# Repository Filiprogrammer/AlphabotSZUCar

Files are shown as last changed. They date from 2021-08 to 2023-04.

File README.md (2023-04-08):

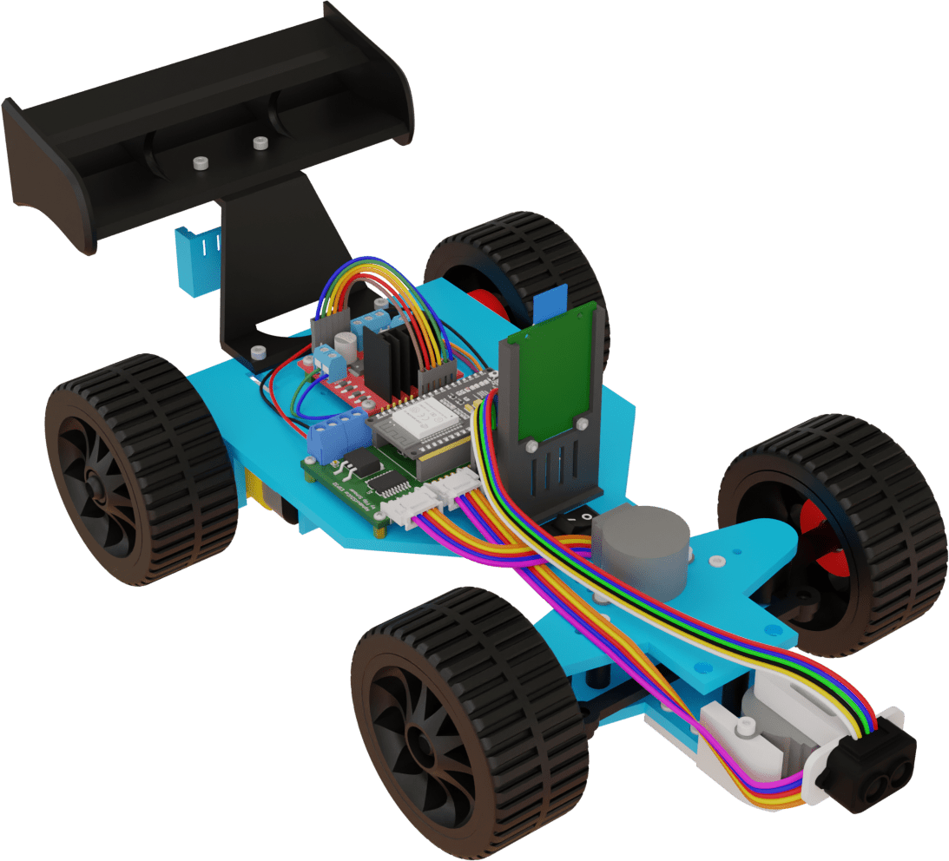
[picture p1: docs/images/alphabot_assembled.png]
Assembled Alphabot


AlphabotSZUCar
==============



The AlphabotSZUCar is a remote-controlled model car with some functions that also let it act autonomously in various ways.

There exist two major variations of this car:

- Controlled by Raspberry Pi 3B/3B+/4B (single-board computer)
- Controlled by ESP32 (microcontroller)

Features
--------

* Communication through WiFi
* Communication through Bluetooth Low Energy
* Remote controlled manual driving
* Obstacle detection & Collision avoidance
* Position and orientation system
* Pathfinding with obstacle avoidance
* Autonomous driving

Building the Alphabot
---------------------

[Alphabot Build Instructions](docs/alphabot_build_instructions.md)

Raspberry Pi variation: Building the software
---------------------------------------------

[Building the software for the Raspberry Pi variation of the Alphabot](docs/alphabot_rpi_software.md)

Emulating the Alphabot
----------------------

[Alphabot Emulation](docs/alphabot_emulation.md)

Connecting to Alphabot with a client
------------------------------------

[Alphabot Client](docs/alphabot_client.md)

Using the Alphabot
------------------

[Alphabot Usage](docs/alphabot_usage.md)

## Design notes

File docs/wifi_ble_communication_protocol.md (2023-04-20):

# 1. WiFi – bit based protocol

All byte sequences (int16, int64...) correspond to the "little-endian" standard.

## 1.1. Packet header

The packet header consists of 1 byte. All following bytes are the payload of the packet.
The last 3 bits (MSB) of the packet header define the protocol version. Currently the only version is 000.

### 1.1.1. Example packet

| Bit 7-5 (MSB) <br> [Version 0] | Bit 4-0 (LSB) <br> [Packet ID 0x01] |
|---|---|
| 0 0 0 | 0 0 0 0 1 |

## 1.2. Requests (Client to Alphabot)

### Speed & Steer (Packet ID: 0x01)

| Field Name | Field Type | Notes |
|---|---|---|
| Speed | int8 | The desired speed (negative values indicate backward driving, positive values indicate forward driving) |
| Steer | int8 | The desired steering direction (negative values indicate left steering, positive values indicate right steering) |

### Calibrate steering (Packet ID: 0x03)

No further data

### Calibrate compass (Packet ID: 0x04)

| Field Name | Field Type | Notes |
|---|---|---|
| Calibration type | uint8 | 0x01 for automatic compass calibration; 0x02 to start manual compass calibration; 0x03 to end manual compass calibration; 0x04 to set compass offset |

### Toggle request (Packet ID: 0x05)

see [3.1. Toggle bit field](#31-toggle---bit-field)

### Ping request (Packet ID: 0x06)

| Field Name | Field Type | Notes |
|---|---|---|
| Timestamp  | int64 | The Unix epoch time in milliseconds when the packet is sent |

### Configure positioning anchors location (Packet ID: 0x07)

| Field Name | Field Type | Notes |
|---|---|---|
| AnchorID | uint8 | The ID of the anchor |
| Position X | int16 | The x coordinate in centimetres |
| Position Y | int16 | The y coordinate in centimetres |

### Set target position for navigation (Packet ID: 0x08)

| Field Name | Field Type | Notes |
|---|---|---|
| Position X | int16 | The x coordinate in centimetres |
| Position Y | int16 | The y coordinate in centimetres |

### Add obstacle (Packet ID: 0x09)

| Field Name | Field Type | Notes |
|---|---|---|
| Position X | int16 | The x coordinate in centimetres |
| Position Y | int16 | The y coordinate in centimetres |
| Width | uint16 | The width in centimetres |
| Height | uint16 | The height in centimetres |

### Remove one obstacle by ID (Packet ID: 0x0A)

| Field Name | Field Type | Notes |
|---|---|---|
| ID | uint16 | ID of the obstacle |

### Remove obstacle by position (Packet ID: 0x0B)

If there are multiple objects in the same position, all of them will be removed.

| Field Name | Field Type | Notes |
|---|---|---|
| Position X | int16 | The x coordinate in centimetres |
| Position Y | int16 | The y coordinate in centimetres |

### Remove all obstacles (Packet ID: 0x0C)

All obstacles (manually added and discovered by the Alphabot) will be removed.

No further data

## 1.3. Responses (Alphabot to client)

### Front distance sensor response (Packet ID: 0x01)

Degree 0 represents the direction, in which the Alphabot is headed towards.
Degree 90 is the right direction.

| Field Name | Field Type | Notes |
|---|---|---|
| Degree | int16 | The degree of the sensor (0-359) |
| Distance | uint16 | The distance in centimetres |

### Positioning response (Packet ID: 0x02)

| Field Name | Field Type | Notes |
|---|---|---|
| Position X | int16 | The x coordinate in centimetres |
| Position Y | int16 | The y coordinate in centimetres |

### Path finding response (Packet ID: 0x03)

| Field Name | Field Type | Notes |
|---|---|---|
| X-start | int8 | X coordinate of the start position in decimeters |
| Y-start | int8 | Y coordinate of the start position in decimeters |
| Path steps data | Path steps data structure | see [Path steps data structure](#33-Path-steps-data-structure) |

### Compass response (Packet ID: 0x04)

The direction is relative to the coordinate system, where +X is right and +Y is down.\
0 degrees indicates the Alphabot is facing in the +X direction.\
90 degrees indicates the Alphabot is facing in the +Y direction.\
180 degrees indicates the Alphabot is facing in the -X direction.\
270 degrees indicates the Alphabot is facing in the -Y direction.

| Field Name | Field Type | Notes |
|---|---|---|
| Degree | int16 | The measured degree (0-359) |

### Ping response (Packet ID: 0x05)

| Field Name | Field Type | Notes |
|---|---|---|
| Timestamp  | int64 | The Unix epoch time in milliseconds when the packet was sent |

### New obstacle registered (Packet ID: 0x06)

| Field Name | Field Type | Notes |
|---|---|---|
| Position X | int16 | The x coordinate in centimetres |
| Position Y | int16 | The y coordinate in centimetres |
| Width | uint16 | The width in centimetres |
| Height | uint16 | The height in centimetres |
| ID | uint16 | The ID of the obstacle |

### Toggle response (Packet ID: 0x07)

The toggle settings get automatically sent upon a new client connection, but they will also be sent if
the Alphabot changes a setting by itself.

see [3.1. Toggle bit field](#31-toggle---bit-field)

### Anchor distance response (Packet ID: 0x08)

| Field Name | Field Type | Notes |
|---|---|---|
| Distance | uint16 | The distance to anchor 0 in centimeters |
| Distance | uint16 | The distance to anchor 1 in centimeters |
| Distance | uint16 | The distance to anchor 2 in centimeters |

### Wheel speed response (Packet ID: 0x09)

| Field Name  | Field Type | Notes |
|---|---|---|
| Speed left  | int8 | The speed of the left wheel in m/s * 100  |
| Speed right | int8 | The speed of the right wheel in m/s * 100 |

### Gyroscope response (Packet ID: 0x0A)

| Field Name | Field Type | Notes |
|---|---|---|
| X-axis | int16 | The speed of the x-axis in degree/s * 10 |
| Y-axis | int16 | The speed of the y-axis in degree/s * 10 |
| Z-axis | int16 | The speed of the z-axis in degree/s * 10 |

### Accelerometer response (Packet ID: 0x0B)

| Field Name | Field Type | Notes |
|---|---|---|
| X-axis | int16 | The acceleration of the x-axis in m/s&#xB2; * 1000 |
| Y-axis | int16 | The acceleration of the y-axis in m/s&#xB2; * 1000 |
| Z-axis | int16 | The acceleration of the z-axis in m/s&#xB2; * 1000 |

### Magnetometer response (Packet ID: 0x0C)

| Field Name | Field Type | Notes |
|---|---|---|
| X-axis | int16 | The magnetic flux density of the x-axis in &#xB5;T * 10 |
| Y-axis | int16 | The magnetic flux density of the y-axis in &#xB5;T * 10 |
| Z-axis | int16 | The magnetic flux density of the z-axis in &#xB5;T * 10 |

### Error message (Packet ID: 0x0D)

| Field Name | Field Type | Notes |
|---|---|---|
| Error ID | uint8 | The error ID, see [3.4.](#34-error-id-format)  |
| Packet header  | uint8 | The packet header that threw the error |
| Payload | uint8 array (0-20) | The payload of the packet that threw the error |

### Back distance sensor response (Packet ID: 0x0E)

Degree 0 represents the opposite direction, in which the Alphabot is headed towards.
Degree 90 is the left direction.

| Field Name | Field Type | Notes |
|---|---|---|
| Degree | int16 | The degree of the sensor (0-359) |
| Distance | uint16 | The distance in centimetres |

# 2. BLE Protocol

### BLE_CHAR_DRIVE_STEER (UUID: a04295f7-eaa8-4536-b3a4-4e7ae4d72dc2)

| Field Name | Field Type | Notes |
|---|---|---|
| Speed | int8 | The desired speed (negative values indicate backward driving, positive values forward driving) |
| Steer | int8 | The desired steering direction (negative values indicate left steering, positive values indicate right steering) |

### BLE_CHAR_PINGCLIENT	(UUID: 117ad3a5-b257-4465-abd4-7dc12a4cf77d)

| Field Name | Field Type | Notes |
|---|---|---|
| Timestamp  | int64 | The Unix epoch time in milliseconds when the packet is sent |

### BLE_CHAR_TOGGLE (UUID: fce001d4-864a-48f4-9c95-de928f1da07b)

| Field Name | Field Type | Notes |
|---|---|---|
| Settings toggle bit field | uint8 | see [3.1.1. Toggle bit field (Settings)](#311-bit-field--1-byte-settings) |
| Logging toggle bit field  | uint8 | see [3.1.2. Toggle bit field (Logging)](#312-bit-field--2-byte-logging) |
| Timestamp | int64 | The Unix epoch time in milliseconds when the packet is sent |

### BLE_CHAR_SENSOR (UUID: 4c999381-35e2-4af4-8443-ee8b9fe56ba0)

see [3.2. Sensor packets](#32-sensor--packets-ble-only)

### BLE_CHAR_TARGET_NAVI (UUID: f56f0a15-52ae-4ad5-bfe1-557eed983618)

| Field Name | Field Type | Notes |
|---|---|---|
| Position X | int16 | The x coordinate in centimetres |
| Position Y | int16 | The y coordinate in centimetres |
| Timestamp  | int64 | The Unix epoch time in milliseconds when the packet is sent |

### BLE_CHAR_CALIBRATE (UUID: d39e8d54-8019-46c8-a977-db13871bac59)

| Field Name | Field Type  | Notes |
|---|---|---|
| Calibration Type | int8 | 0x00 to calibrate steering; 0x01 for automatic compass calibration; 0x02 to start manual compass calibration; 0x03 to end manual compass calibration; 0x04 to set compass offset |
| Timestamp | int64 | The Unix epoch time in milliseconds when the packet is sent |

### BLE_CHAR_ADD_OBSTACLE (UUID: 60db37c7-afeb-4d40-bb17-a19a07d6fc95)

At first position, width and height is sent by the client, the Alphabot will answer with the data and the ID.

| Field Name | Field Type | Notes |
|---|---|---|
| Timestamp  | int64 | The Unix epoch time in milliseconds when the packet is sent |
| Position X | int16 | The x coordinate in centimetres |
| Position Y | int16 | The y coordinate in centimetres |
| Width | uint16 | The width in centimetres |
| Height | uint16 | The height in centimetres |
| ID | uint16 | The ID of the obstacle (gets set by the Alphabot) |

### BLE_CHAR_REMOVE_OBSTACLE (UUID: 6d43e0df-682b-45ef-abb7-814ecf475771)

Obstacles can be removed either by ID or by position.
If the characteristic is 0 bytes long, ALL obstacles will be removed.
If the characteristic is 10 bytes long, the value is interpreted as the obstacle ID.
If the characteristic is 12 bytes long, the values are interpreted as the position.
The Alphabot will send the corresponding packet when the removal of obstacles is completed.
If there are multiple objects on the same position, all of them will be removed.

| Field Name | Field Type | Notes |
|---|---|---|
| Timestamp  | int64 | The Unix epoch time in milliseconds when the packet is sent |
| ID | uint16 | The ID of the obstacle |

#### OR

| Field Name | Field Type | Notes |
|---|---|---|
| Timestamp  | int64 | The Unix epoch time in milliseconds when the packet is sent |
| Position X | int16 | The x coordinate in centimetres |
| Position Y | int16 | The y coordinate in centimetres |

### BLE_CHAR_PATH_FINDING (UUID: 8dad4c9a-1a1c-4a42-a522-ded592f4ed99)

| Field Name | Field Type | Notes |
|---|---|---|
| X-start | int8 | X coordinate of the start position in decimeters |
| Y-start | int8 | Y coordinate of the start position in decimeters |
| Path steps data | Path steps data structure | see [Path steps data structure](#33-Path-steps-data-structure) |

### BLE_CHAR_ANCHOR_LOCATIONS (UUID: 8a55dd30-463b-40f6-8f21-d68efcc386b2)

| Field Name | Field Type | Notes |
|---|---|---|
| Timestamp  | int64 | The Unix epoch time in milliseconds when the packet is sent |
| Position X | int16 | The x coordinate in centimetres of anchor 0 |
| Position Y | int16 | The y coordinate in centimetres of anchor 0 |
| Position X | int16 | The x coordinate in centimetres of anchor 1 |
| Position Y | int16 | The y coordinate in centimetres of anchor 1 |
| Position X | int16 | The x coordinate in centimetres of anchor 2 |
| Position Y | int16 | The y coordinate in centimetres of anchor 2 |

### BLE_CHAR_ANCHORS_DISTANCES (UUID: 254492a2-9324-469b-b1e2-4d4590972c35)

| Field Name | Field Type | Notes |
|---|---|---|
| Distance | uint16 | The distance to anchor 0 in centimetres |
| Distance | uint16 | The distance to anchor 1 in centimetres |
| Distance | uint16 | The distance to anchor 2 in centimetres |

### BLE_CHAR_IMU (UUID: 93758afa-ce6f-4670-9562-ce92bda84d49)

| Field Name | Field Type | Notes |
|---|---|---|
| Type | int8 | Indicates whether the packet is a gyroscope-package (value 0), an accelerometer-package (value 1), or an magnetometer-package (value 2) |
| x-Axis | int16 | The value of the x-Axis |
| y-Axis | int16 | The value of the y-Axis |
| z-Axis | int16 | The value of the z-Axis |

### BLE_CHAR_WHEEL_SPEED (UUID: 8efafa16-15de-461f-bde1-493261201e2b)

| Field Name  | Field Type | Notes |
|---|---|---|
| Speed left  | int8 | The speed of the left wheel in m/s * 100  |
| Speed right | int8 | The speed of the right wheel in m/s * 100 |

### BLE_CHAR_ERROR (UUID: dc458f08-ea3e-4fe1-adb3-25c840be081a)

If the original payload was 19 or 20 bytes long, the last one or two bytes won't be shown.

| Field Name | Field Type | Notes |
|---|---|---|
| Error ID | uint8 | The error ID, see [3.4.](#34-error-id-format) |
| BLE CHAR ID | uint8 | The first byte of the BLE characteristic UUID that threw the error |
| Payload | uint8 array (0-18) | The payload of the packet that threw the error |

# 3. Bit fields

## 3.1. Toggle - Bit field

In the WiFi protocol, the packet 0x05 is followed by a 2-byte bit field.
In the BLE protocol it is a characteristic which is 10 bytes in size, because the timestamp (8 bytes) is sent right after the actual bit field (2 bytes)
This bit field allows various settings to be switched on or off. If a 0 is sent,
that setting is going to be deactivated, if a 1 is sent it is going to be activated.
General settings are sent in the 1st byte. 
The 2nd byte changes certain logging options.

### 3.1.1. Bit field – 1. Byte (Settings)

| Bit 7 (MSB) | Bit 6 | Bit 5 | Bit 4 | Bit 3 | Bit 2 | Bit 1 | Bit 0 (LSB) |
|---|---|---|---|---|---|---|---|
| Invite | Positioning | Collision Avoidance | Navigation-Mode | Explore-Mode | not used | not used | not used |

### 3.1.2. Bit field – 2. Byte (Logging)

| Bit 7 (MSB) | Bit 6 | Bit 5 | Bit 4 | Bit 3 | Bit 2 | Bit 1 | Bit 0 (LSB) |
|---|---|---|---|---|---|---|---|
| Positioning | Obstacle distance | Pathfinder path | Compass direction | Anchor distances | Wheel speed | Inertial Measurement Unit | not used |

## 3.2. Sensor – Packets (BLE only)

The first two bytes describe the sensor types that will follow. Then the payload of these packets will follow. There can be multiple sensor responses sent at a time. The following responses can be sent in one packet:

### Example bit stream

In the first byte 0b01 is sent twice, because two front distance sensor packets will follow. The following bits in the first two bytes do not matter in this case, because the bit stream does not contain more sensor data. Byte 2 and 3 represent the payload of the first distance sensor data. Byte 4 and 5 represent the payload of the second distance sensor data.

| Byte 0 | Byte 1 | Byte 2 | Byte 3 | Byte 4 | Byte 5 |
|---|---|---|---|---|---|
| 00000101 | 00000000 | 00000101 | 10000000 | 01100100 | 10000001 |

### Back distance sensor response (Sensor type: 0b00)

Degree 0 represents the opposite direction, in which the Alphabot is headed towards.
Degree 90 is the left direction.

| Field Name | Field Type | Notes |
|---|---|---|
| Degree | int8 | The degree of the sensor (-128-127) |
| Distance | uint8 | The distance in centimetres divided by 2 |

### Front distance sensor response (Sensor type: 0b01)

Degree 0 represents the direction, in which the Alphabot is headed towards.
Degree 90 is the right direction.

| Field Name | Field Type | Notes |
|---|---|---|
| Degree | int8 | The degree of the sensor (-128-127) |
| Distance | uint8 | The distance in centimetres divided by 2 |

### Positioning response (Sensor type: 0b10)

The position will be split into 3 bytes, 12 bit per coordinate

| Field Name | Field Type | Notes |
|---|---|---|
| Position X | int12 | The x coordinate in centimetres |
| Position Y | int12 | The y coordinate in centimetres |

### Compass response (Sensor type: 0b11)

The direction is relative to the coordinate system, where +X is right and +Y is down.\
0 degrees indicates the Alphabot is facing in the +X direction.\
90 degrees indicates the Alphabot is facing in the +Y direction.\
180 degrees indicates the Alphabot is facing in the -X direction.\
270 degrees indicates the Alphabot is facing in the -Y direction.

| Field Name | Field Type | Notes |
|---|---|---|
| Degree | int16 | The measured degree (0-359) |

## 3.3. Path steps data structure

The Path steps data structure contains a list of steps in certain directions which together form a path.
The length of the data structure can be anywhere between 1 to 18 bytes long.
The first 6 bits of the first byte contain the number of the following path steps.
Note that bit 0 refers to the least significant bit.
The path steps are stored such that several entries are within a single byte and sometimes an entry overlaps between multiple bytes.
The first entry is stored in bits 6 and 7 of the first byte and in bit 0 of the second byte.
Bits 1 to 3 of the second byte are the second entry, bits 4 to 6 are the third entry, and so on.
With 3 bits per path step there are 8 possible values. The format of a path step is described in [Path step format](#331-Path-step-format)

### 3.3.1. Path step format

| Encoded value | Direction  |
|---|---|
| 0 | left-up |
| 1 | left |
| 2 | left-down  |
| 3 | up |
| 4 | right-down |
| 5 | down |
| 6 | right-up |
| 7 | right |

### 3.3.2. Example bit stream

The following example shows a possible bit stream of the path finding data. In the [example encoded in bytes](#333-example-encoded-in-bytes) all steps are explained explicitly.

<span style="color:#f53d3d">001000</span>
| <span style="color:#f5993d">001</span>
| <span style="color:#f5f53d">010</span>
| <span style="color:#99f53d">101</span>
| <span style="color:#3df53d">101</span>
| <span style="color:#3df599">100</span>
| <span style="color:#3df5f5">100</span>
| <span style="color:#3d99f5">111</span>
| <span style="color:#3d3df5">111</span>
| 00

### 3.3.3. Example encoded in bytes

<span style="color:#f5993d">01</span><span style="color:#f53d3d">001000</span>
<span style="color:#3df53d">1</span><span style="color:#99f53d">101</span><span style="color:#f5f53d">010</span><span style="color:#f5993d">0</span>
<span style="color:#3df5f5">100</span><span style="color:#3df599">100</span><span style="color:#3df53d">10</span>
00<span style="color:#3d3df5">111</span><span style="color:#3d99f5">111</span>

| Binary value of step | Step direction |
|---|---|
| <span style="color:#f53d3d">001000</span> | Number of path steps = 8 |
| <span style="color:#f5993d">001</span> | left |
| <span style="color:#f5f53d">010</span> | left-down |
| <span style="color:#99f53d">101</span> | down |
| <span style="color:#3df53d">101</span> | down |
| <span style="color:#3df599">100</span> | right-down |
| <span style="color:#3df5f5">100</span> | right-down |
| <span style="color:#3d99f5">111</span> | right |
| <span style="color:#3d3df5">111</span> | right |

## 3.4. Error id format

| Encoded value | Error |
|---|---|
| 0x00 | unknown error |
| 0x01 | unknown protocol |
| 0x02 | known but not supported protocol  |
| 0x03 | unknown packet ID |
| 0x04 | wrong payload |

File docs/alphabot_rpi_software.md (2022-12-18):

# Building the software for the Raspberry Pi variation of the Alphabot

## Prerequisites

Make sure that you have at least 3GB of free storage space.

Make sure that you have installed the following prerequisites:

* Docker - [Docker Engine Install Instructions](https://docs.docker.com/engine/install/)
* parted

Debian:

```console
sudo apt-get install parted
```

Arch Linux:

```console
sudo pacman -Sy parted
```

Fedora:

```console
sudo yum install parted
```

* kpartx

Debian:

```console
sudo apt install kpartx
```

Arch Linux:

```console
sudo pacman -Sy multipath-tools
```

Fedora:

```console
sudo yum install kpartx
```

## Build Image

```console
sudo rpi/sd_image/build.sh
```

## Running on real hardware

Flash rpi/sd_image/raspi_alphabot.img onto an SD card with a size of at least 1GiB. Plug the flashed SD card into your Raspberry Pi 3B/3B+/4B.

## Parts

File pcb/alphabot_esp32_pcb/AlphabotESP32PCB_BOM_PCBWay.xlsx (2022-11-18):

 |  |  | BOM
Item # | *Designator | *Qty | Manufacturer | *Mfg Part # | Description / Value | *Package/Footprint | Type | Your Instructions / Notes
1 | ICMU1 | 1 | TDK InvenSense | ICM-20948 | IMU ACCEL/GYRO/COMPI2C/SPI 24QFN | 24QFN | SMD | Pin 1 is on the left side. It is intentional that there is no pad on the PCB for the exposed die pad on the center of the chip.
2 | C1,C4 | 2 | KEMET | C0603C104K3RAC7013 | CAP CER 0.1uF ±10% 25V X7R | 0603 | SMD
3 | C2 | 1 | KEMET | C0603C106M8PAC7411 | CAP CER 10uF ±20% 10V X5R | 0603 | SMD
4 | ICMC1 | 1 | KEMET | C0805C104K5RAC7411 | CAP CER 0.1uF ±10% 50V X7R | 0805 | SMD
5 | Q1,Q3,Q4 | 3 | ON Semiconductor | BSS138 | MOSFET N-CH 50V 220MA SOT23-3 | SOT-23-3 | SMD
6 | R1 | 1 | Vishay / Dale | CRCW06031K00FKEA | RES 1.0K OHM 1/10W 1% | 0603 | SMD
7 | R2 | 1 | Vishay / Dale | CRCW06032K20FKEA | RES 2.2K OHM 1/10W 1% | 0603 | SMD
8 | R5,R6,R7,R11 | 4 | Vishay / Dale | CRCW060310K0FKEA | RES 10K OHM 1/10W 1% | 0603 | SMD
9 | R9,R10 | 2 | Vishay / Dale | CRCW06034K70FKEA | RES 4.7K OHM 1/10W 1% | 0603 | SMD
10 | U1 | 1 | Microchip Technology / Micrel | MIC5225-1.8YM5-TR | IC REG LINEAR 1.8V 150MA SOT-23-5 | SOT-23-5 | SMD
11 | U2 | 1 | UTD Semiconductor | ULN2803A | SOP-18 DARLINGTON TRANSISTOR ARR | 18-SOP | SMD
12 | U4 | 1 | STMicroelectronics (https://www.mouser.at/manufacturer/stmicroelectronics/) | L7805ACD2T-TR | IC REG LINEAR 5V 1.5A D2PAK | D2PAK | SMD
13 | C3 | 1 | KEMET | C0603C331K5RAC7867 | CAP CER 330PF 50V X7R 0603 | 0603 | SMD

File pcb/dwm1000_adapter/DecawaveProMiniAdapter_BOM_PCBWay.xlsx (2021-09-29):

 |  |  | BOM
Item # | *Ref Des | *Qty | Manufacturer | *Mfg Part # | Description / Value | *Package | Type | Your Instructions / Notes
1 | U1,U2,U3 | 3 | Texas Instruments | SN74LVC2G17DBVRG4 | IC BUF NON-INVERT 5.5V | SOT-23-6 | SMD | Align dot on chip with dot on PCB (pin 1)
2 | C1,C3 | 2 | Wurth Elektronik | 885012206071 | CAP CER 0.1uF ±10% 25V X7R | 0603 | SMD
3 | C2,C4,C5 | 3 | Yageo | CC0603ZRY5V7BB105 | CAP CER 1uF -20%, +80% 16V Y5V | 0603 | SMD
4 | R1 | 1 | Vishay / Dale | CRCW06031K00FKEA | RES 1.0K OHM 1/10W 1% | 0603 | SMD
5 | R2 | 1 | Vishay / Dale | CRCW060310K0FKEA | RES 10K OHM 1/10W 1% | 0603 | SMD
6 | LDO | 1 | Diodes Incorporated | AP7333-33SRG-7 | IC REG LIN 3.3V 300MA SOT23R-3 | SOT-23R-3 | SMD
7 | D1 | 1 | Lite-On Inc. | LTST-C191KGKT | Green 571nm LED Indication - Discrete 2V 0603 | 0603 | SMD
8 | J1 | 1 | TE Connectivity AMP Connectors | 1734035-4 | CONN RCPT USB2.0 MINI B SMD R/A |  | SMD
9 | DWM1000 | 1 | Decawave | DWM1000 | IC RF-Module UWB Transceiver |  | SMD

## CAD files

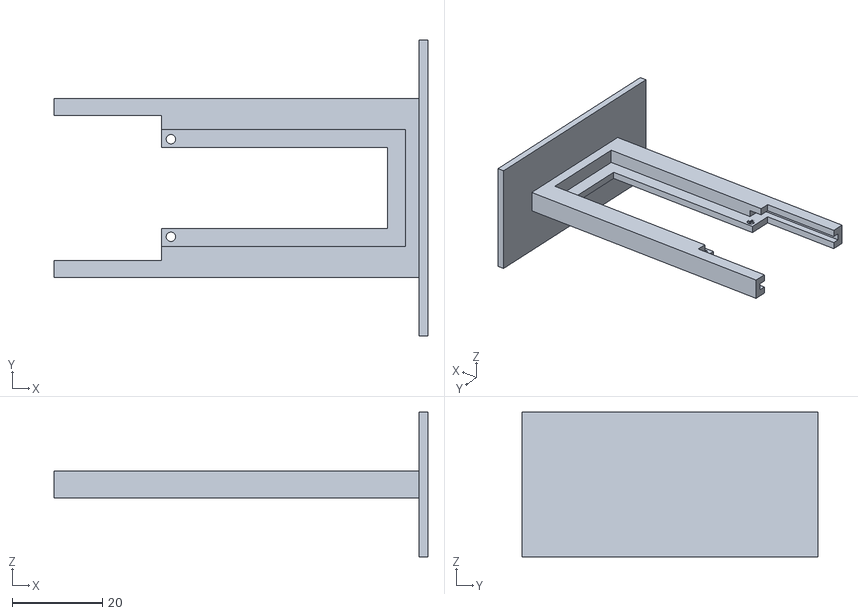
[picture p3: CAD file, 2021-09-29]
stl/dwm1000.anchor.adapter.board.mount.stl
82.8 x 65.6 x 32.0

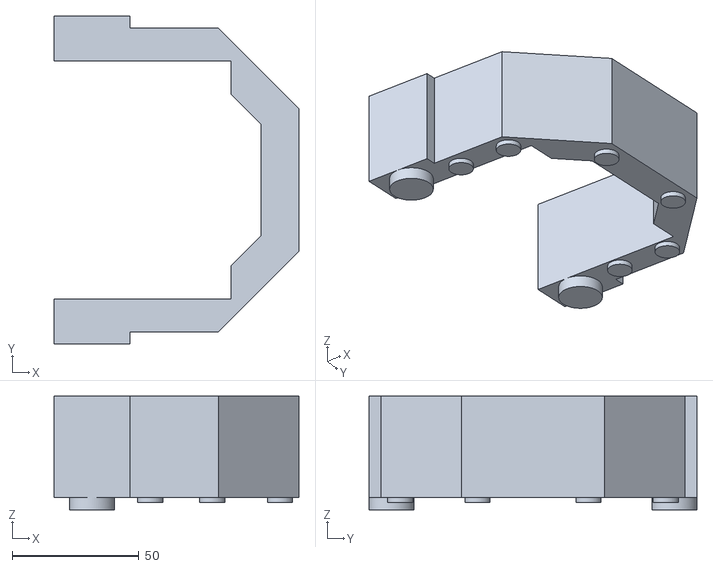
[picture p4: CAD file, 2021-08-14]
stl/stand/alphabot.stand.V3.stl
96.8 x 129.5 x 45.0

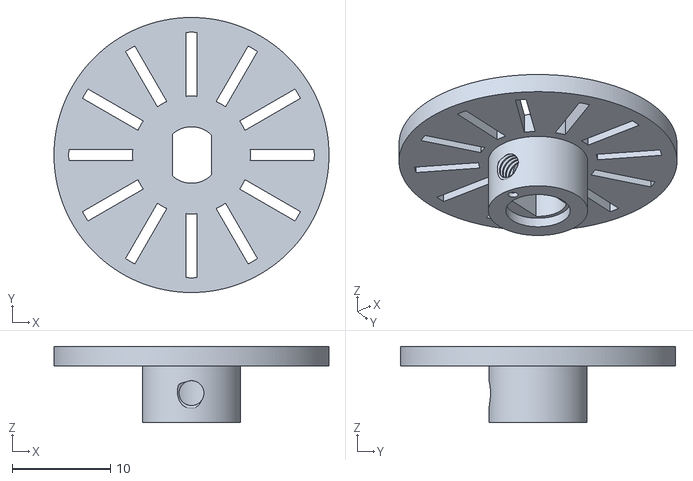
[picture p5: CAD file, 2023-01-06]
stl/vehicle/addon/wheel.encoder.stl
28.0 x 28.0 x 7.75

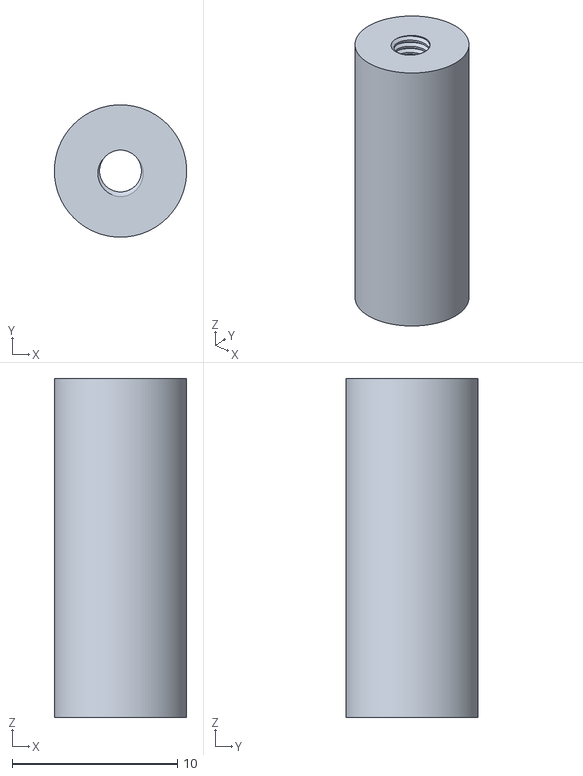
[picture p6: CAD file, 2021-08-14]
stl/vehicle/base/frontwheel.suspension.distance.stl
8.00 x 8.00 x 20.5

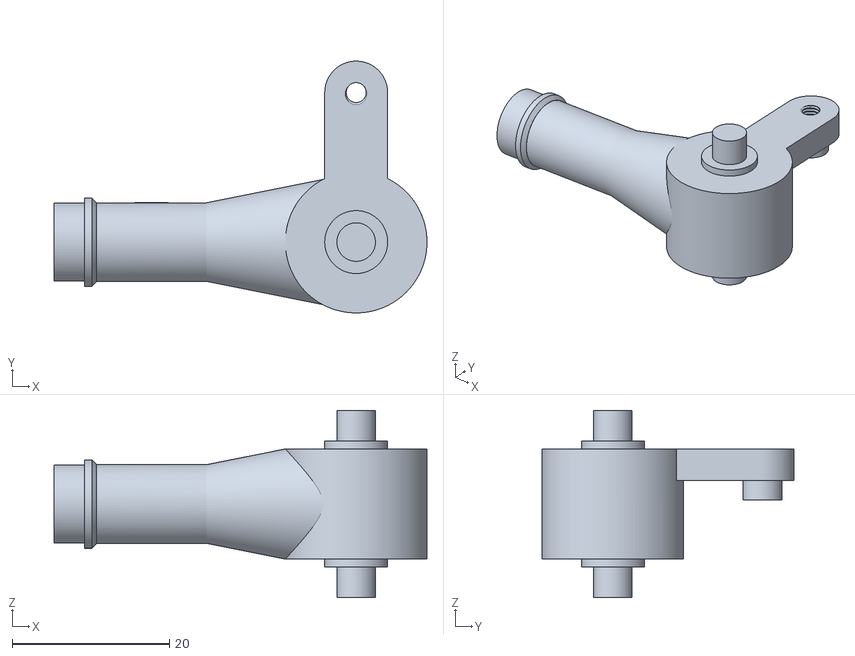
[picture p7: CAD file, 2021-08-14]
stl/vehicle/steering/suspension.right.V4.stl
47.4 x 32.0 x 23.8

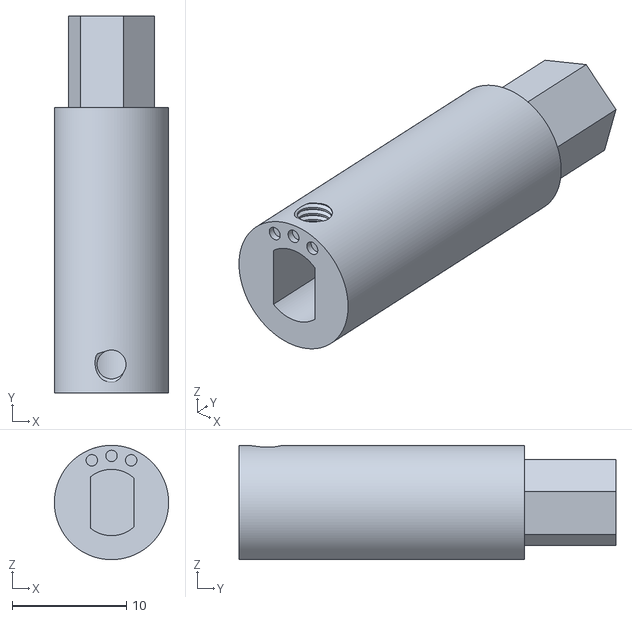
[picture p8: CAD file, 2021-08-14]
stl/vehicle/wheel/rim.axle.back.xl.stl
10.00 x 33.0 x 10.00

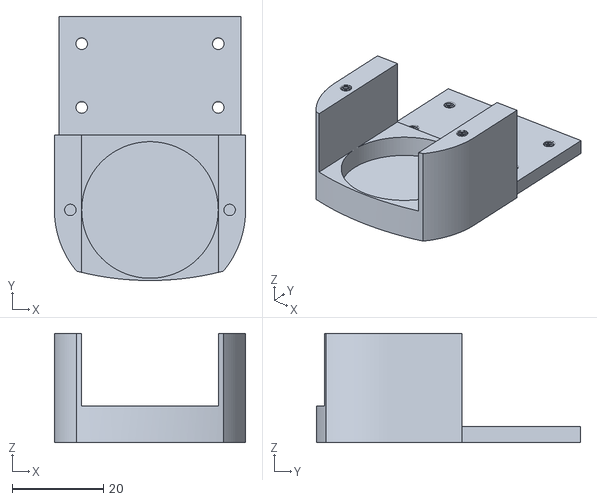
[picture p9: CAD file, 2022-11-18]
stl/vehicle/addon/bumper.lidar.front.stl
42.0 x 58.0 x 24.0

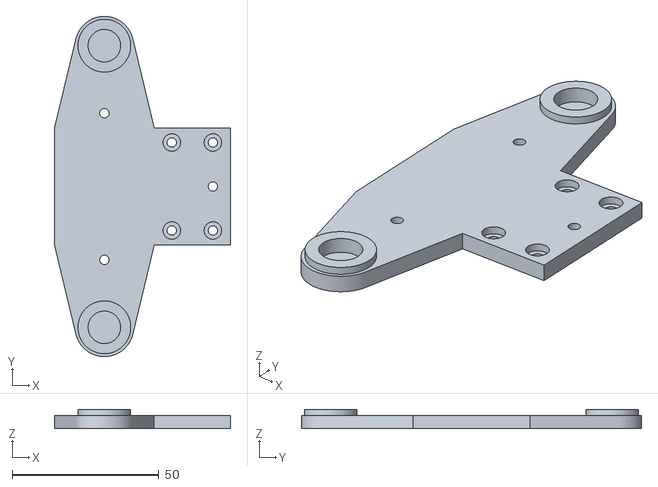
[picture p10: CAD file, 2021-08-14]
stl/vehicle/base/alphabot.4Wheel.base.suspension.V6.stl
60.0 x 116.0 x 6.50

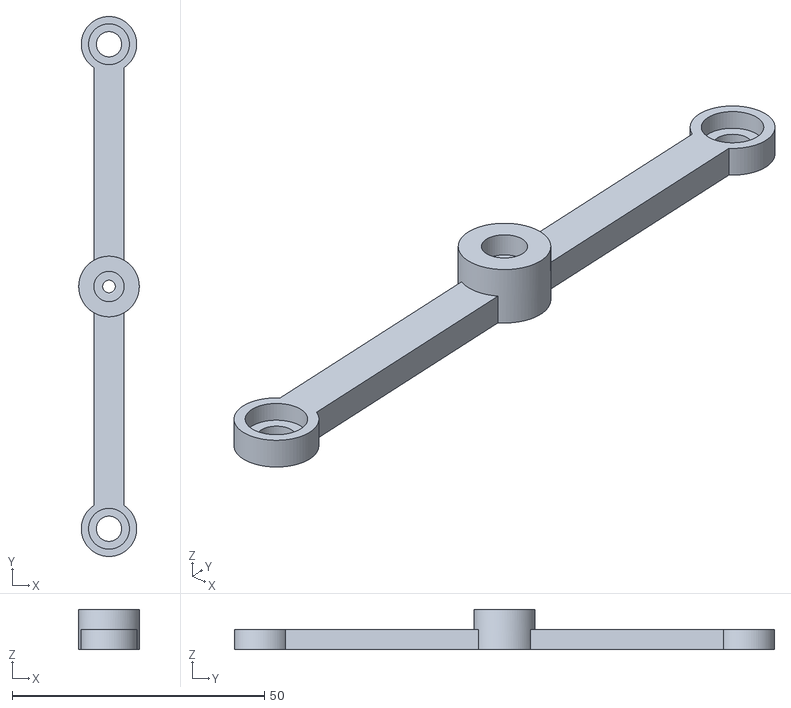
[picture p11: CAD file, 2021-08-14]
stl/vehicle/steering/steering.axle.stl
12.0 x 107.0 x 8.00

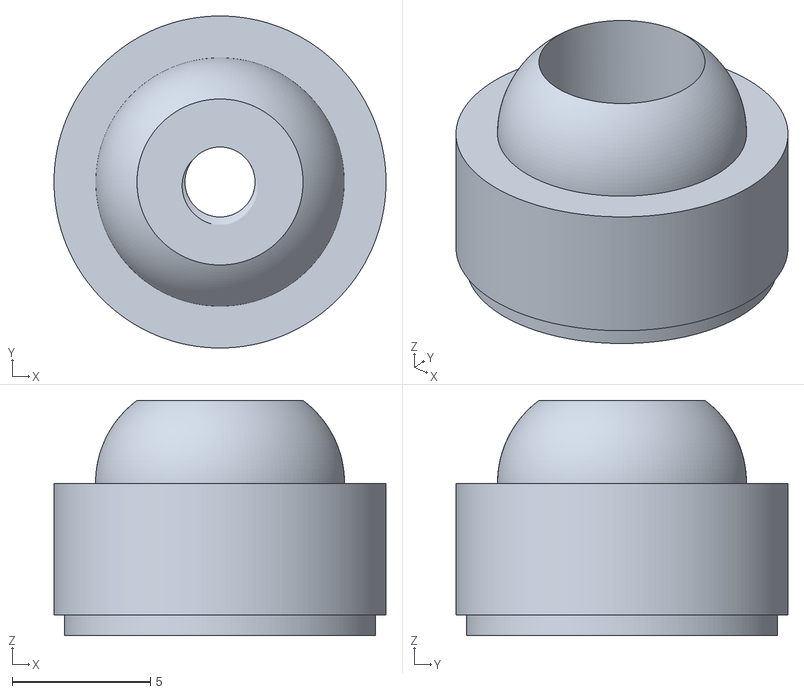
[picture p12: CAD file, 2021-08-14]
stl/vehicle/wheel/rim.62mm.front.nut.stl
12.0 x 12.0 x 8.50

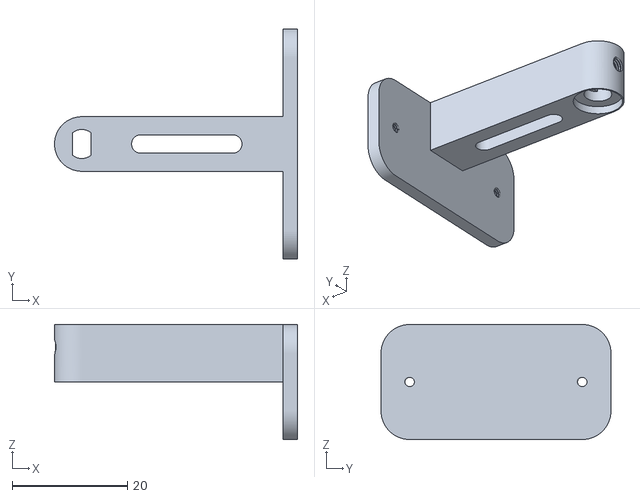
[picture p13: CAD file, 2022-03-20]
stl/vehicle/addon/bumper.lidar.holder.stl
42.2 x 40.0 x 20.0

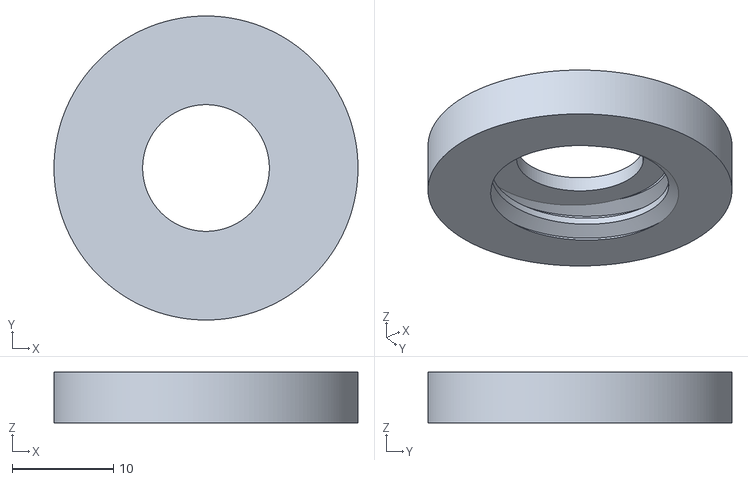
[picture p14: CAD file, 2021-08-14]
stl/vehicle/wheel/rim.62mm.front.bearing.cage.V2.stl
30.0 x 30.0 x 5.00

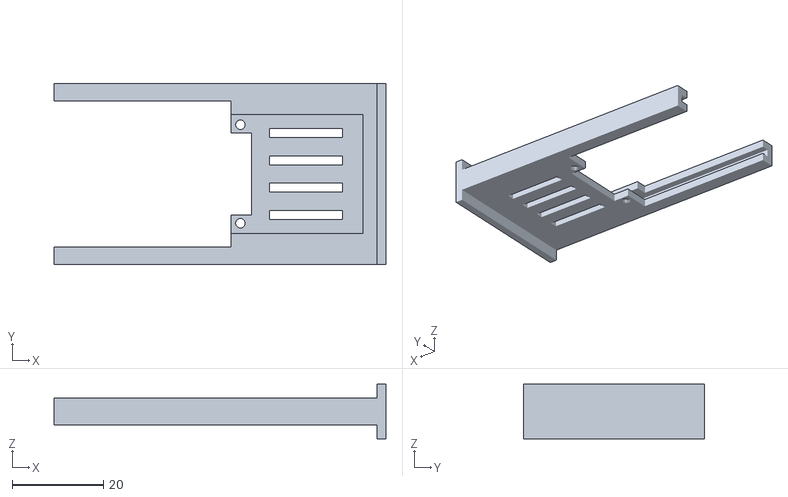
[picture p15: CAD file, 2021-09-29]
stl/vehicle/addon/dwm1000.tag.adapter.board.mount.stl
72.8 x 39.6 x 12.0

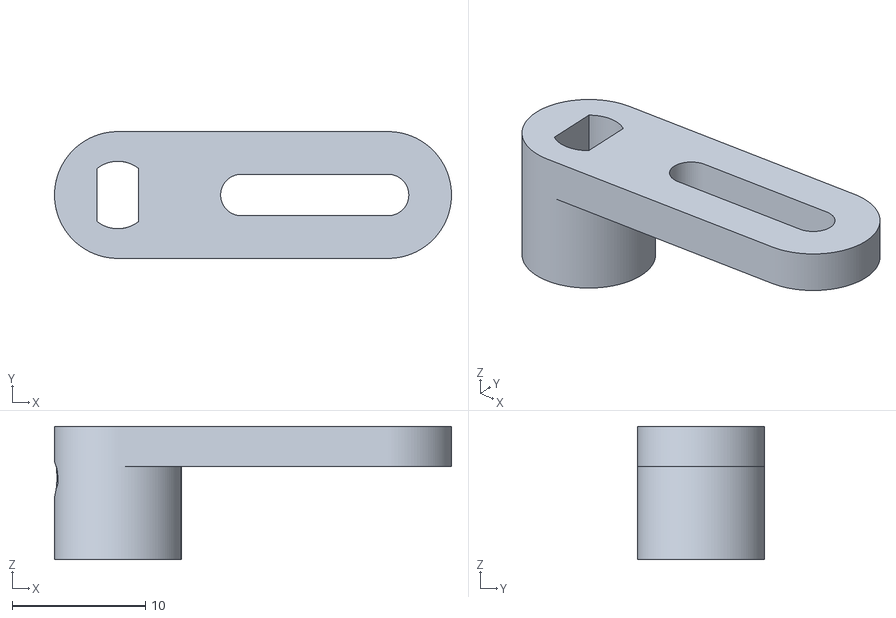
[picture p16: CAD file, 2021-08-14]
stl/vehicle/steering/steering.stepper.pin.stl
29.8 x 9.50 x 10.0

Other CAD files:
stl/vehicle/steering/suspension.left.V4.stl
stl/vehicle/wheel/rim.62mm.back.bearing.cage.V2.stl
stl/vehicle/addon/bumper.hc-sr04.front.V3.stl
stl/vehicle/steering/steering.stepper.pin.xl.stl
stl/vehicle/addon/cable.stop.top.stl
stl/vehicle/addon/gy-271.holder.stl
stl/vehicle/addon/hc-sr04.holder.stl
stl/vehicle/addon/hc-sr04.square.top.mount.single.stl
stl/vehicle/addon/raised.holder.stl
stl/vehicle/addon/wing.holder.V4.hc-sr04.stl
stl/vehicle/addon/wing.holder.V5.50mm.stl
stl/vehicle/addon/wingv4.stl
stl/vehicle/wheel/rim.axle.back.l.stl
stl/vehicle/wheel/rim.axle.back.m.stl
stl/vehicle/wheel/rim.axle.back.stl
stl/vehicle/wheel/rim.back.62mm.V2.stl
stl/vehicle/wheel/rim.front.62mm.V2.stl
stl/vehicle/wheel/tire.base.62.78.stl

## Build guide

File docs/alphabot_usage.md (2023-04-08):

# Alphabot Usage

Once the Alphabot has been built and the Android client deployed to a mobile device, a number of use cases open up.

## Connecting the client to the Alphabot

Turn the Alphabot on by flipping the switch on the vehicle into the 1 state. Now the front wheels and the front sensor should start calibrating.

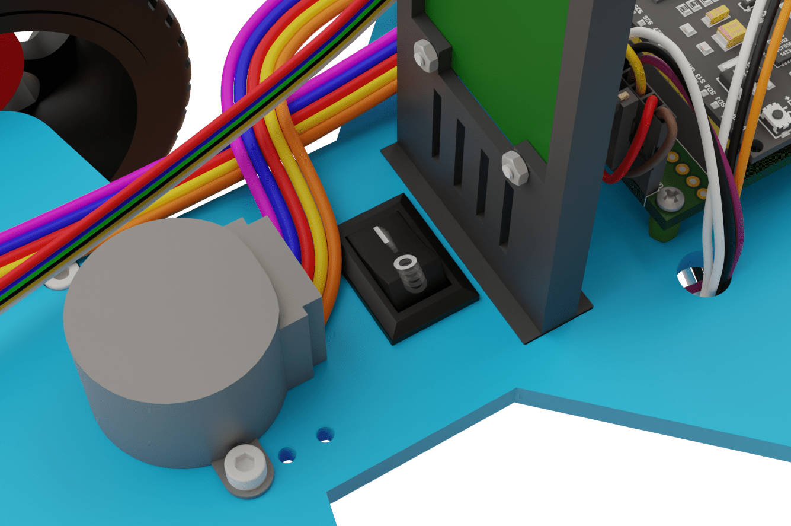
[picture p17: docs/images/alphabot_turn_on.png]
Turning the Alphabot on


Start the android client and type the BLE MAC address of the ESP32 on the Alphabot into the text box and then press the connect button. After one or two seconds the control activity should open up.

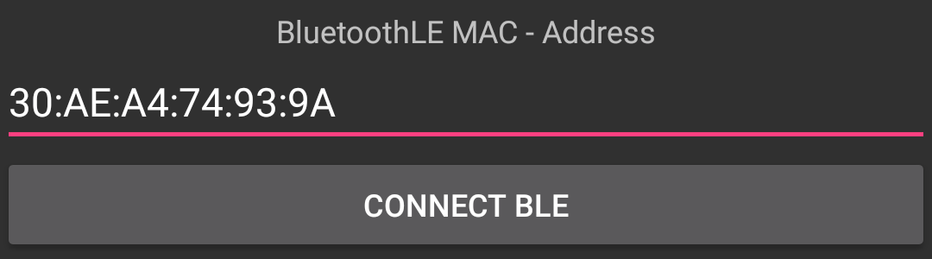
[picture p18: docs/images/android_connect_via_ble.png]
Connect the Android client to the Alphabot via BLE


## Explaining the basic controls

What should be immediately apparent, is that tilting the phone steers the front wheels of the car.

Disabling collision avoidance grants the user unrestricted control over the movement of the vehicle. Holding down the "Accelerate" button makes the vehicle accelerate forwards. The longer that button is held down, the faster the vehicle gets. Upon releasing the button the vehicle starts slowing down. To maintain a slow speed forwards, the "Accelerate" button has to be pushed and released in regular intervals. If the user wishes to stop the car abruptly, they can do so by briefly pressing the "Brake" button. The "Brake" button can also be used the same way as the "Accelerate" button to drive backwards. The "Accelerate" button also stops a vehicle that is driving backwards. The desired speed is shown as a progress bar above the two buttons.

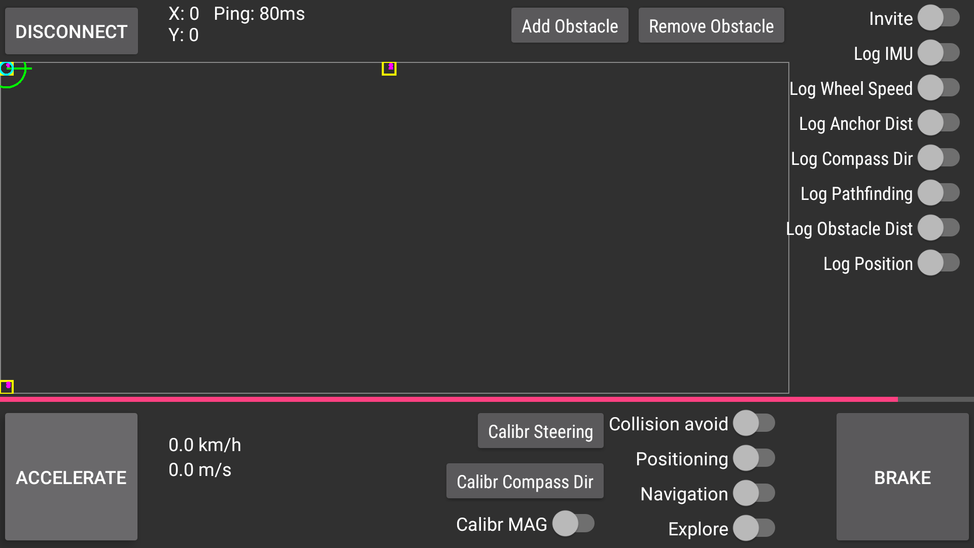
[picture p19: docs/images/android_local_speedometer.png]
Local speedometer in the Android client


Enabling the "Log wheel speed" switch displays the mean wheel speed to the right of the "Accelerate" button. The actual speed of the rear wheels is also indicated by two progress bars just above the magenta progress bar. The faster the wheels get, the more the bars fill towards the center of the screen. The left bar represents the left rear wheel and the right bar represents the right rear wheel.

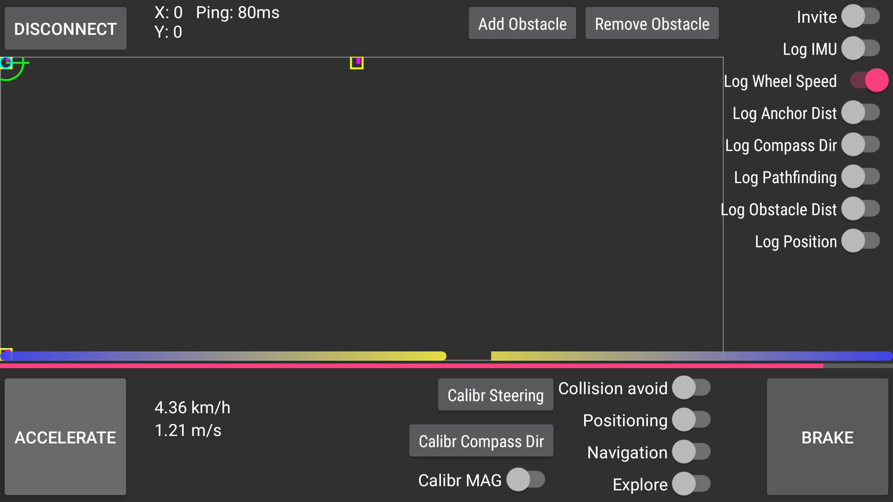
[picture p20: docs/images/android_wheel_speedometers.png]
Wheel speedometers in the Android client


## Using the compass to determine the direction of the vehicle

Enabling the "Log Compass Dir" switch makes the vehicle on the minimap face into the same direction as the Alphabot. Odds are, that the displayed direction is incorrect. To fix this, the magnetometer first needs to be calibrated. To do that, place the vehicle on a flat surface away from any magnetic interferences. Then enable the "Calibr MAG" switch. Now drive the vehicle in a circle a few times or simply rotate it by hand, making sure it always lies flat on the ground. Once that is done, disable the "Calibr MAG" switch. Now the measured direction should rotate proportionally to the rotation of the vehicle. However, the direction is probably offset by some number of degrees from the user's desired direction. Here the user should decide how to setup a positioning system and relative to that in which direction the vehicle should face.

## Setting up the positioning system

First the user should decide where to set up the positioning system and then place the anchors far apart from each other. It is important that the anchors do not all reside on one line.

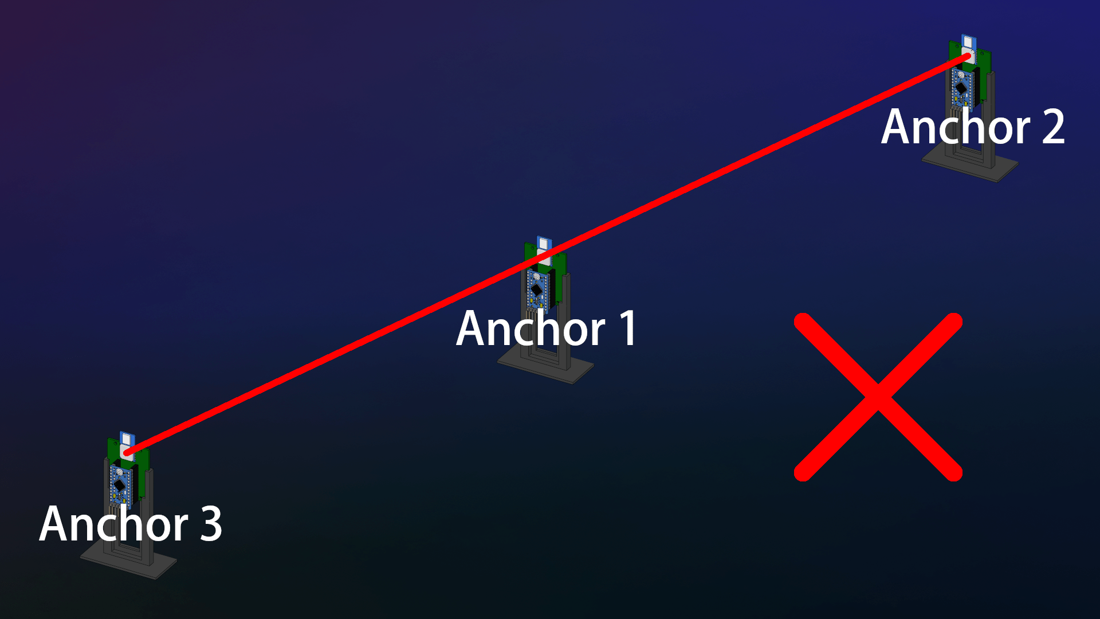
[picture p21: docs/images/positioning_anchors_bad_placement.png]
Positioning anchors should not all reside on one line


 A recommended way to place the anchors can be seen in the following picture:

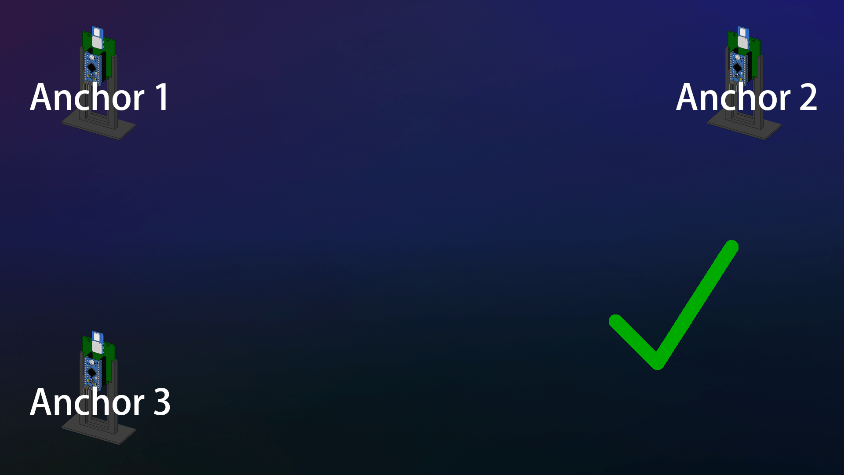
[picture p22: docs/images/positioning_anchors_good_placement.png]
Recommended way to place the positioning anchors


Once the user has decided where to place the anchors, it is important to ensure that the anchors remain in place without moving. In the next step the positions of the anchors should be measured. It is important that the measurements are as accurate as possible. This should result in every anchor having its own coordinates.

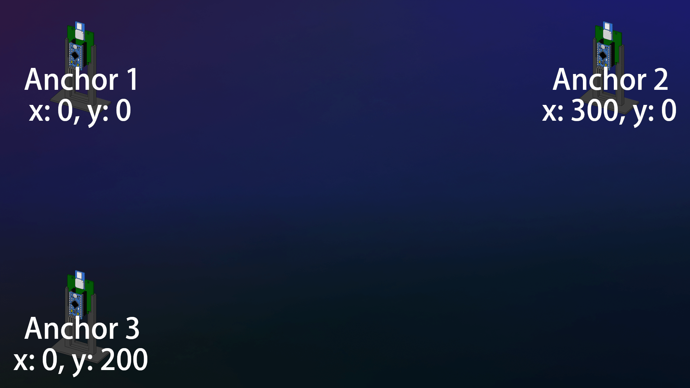
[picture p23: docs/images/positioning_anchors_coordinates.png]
Positioning anchors with coordinates


Now power on the positioning anchors, turn on the Alphabot and connect to it. Once connected enable the "Positioning" switch. A dialog should appear asking for the anchor coordinates.

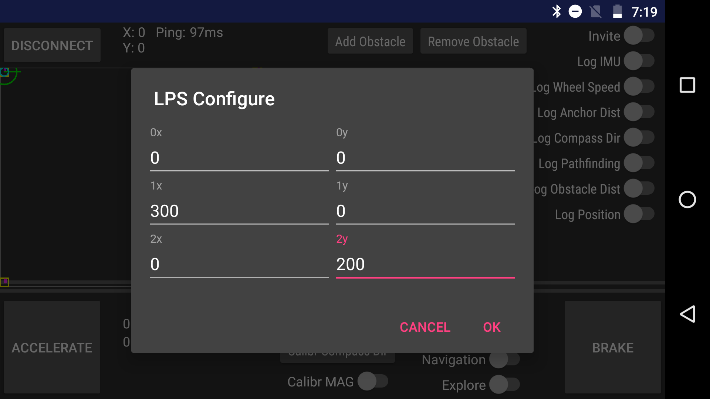
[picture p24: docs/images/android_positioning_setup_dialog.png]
Positioning setup dialog in the Android client


Enter the anchor coordinates and press "OK". This enables the positioning system. Enable the "Log Position" switch to see the estimated position. The coordinates of the vehicle are displayed next to the "Disconnect" button and it is also visually represented on the map in the middle of the screen.

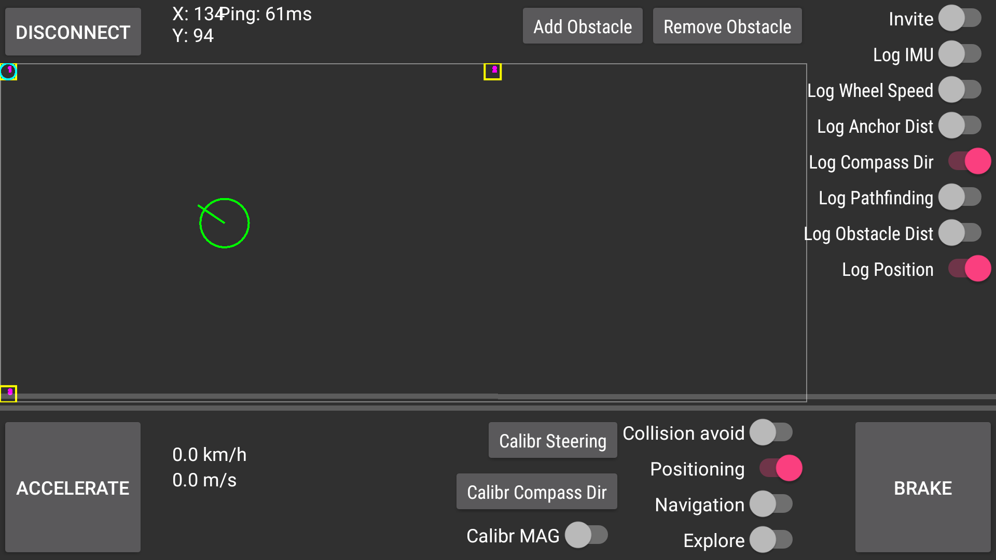
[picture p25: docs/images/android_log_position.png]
Show the position in the Android client


To make the compass point in the correct direction, first make sure that "Log Compass Dir" is enabled. Then place the vehicle anywhere on the map facing the first anchor. Make sure that it is pointing as accurately as possible in the direction of the first anchor. Wait a few seconds to ensure that the estimated position is as close to the truth as possible. Then press the "Calibr Compass Dir" button. The measured direction should now match the truth.

With the compass properly calibrated, the positioning system should now work very accurately while driving around.

## Navigation

By enabling the "Navigation" switch, the Alphabot is put into navigation mode. The user can no longer directly control the vehicle. Instead the user can click anywhere on the map and the Alphabot is going to try to drive toward that location. To see the path that the Alphabot is trying to take, enable the "Log Pathfinding" switch.

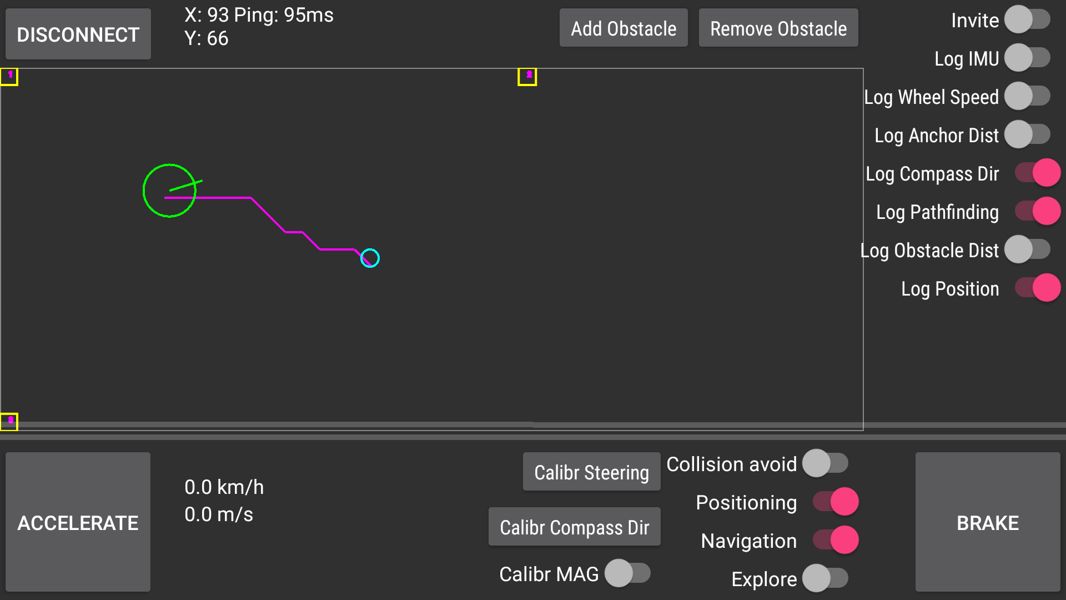
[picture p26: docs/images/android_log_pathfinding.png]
Log pathfinding in the Android client


## Obstacles

In case there are any obstacles that the vehicle should avoid, those can be added manually via the "Add Obstacle" button. Pressing the button opens a dialog where the user can enter the position and size of the obstacle.

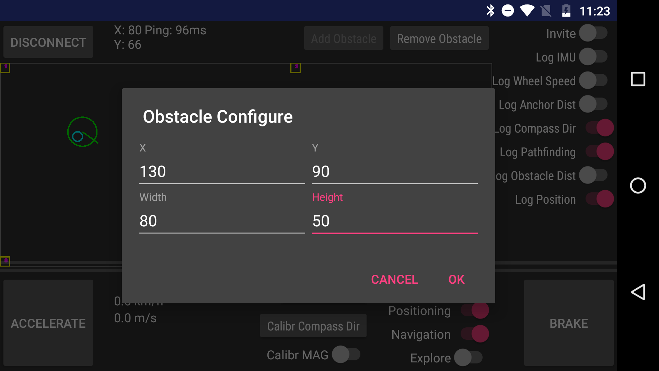
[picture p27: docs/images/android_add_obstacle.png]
Add an obstacle in the Android client


Pressing "OK" adds the obstacle to the map.

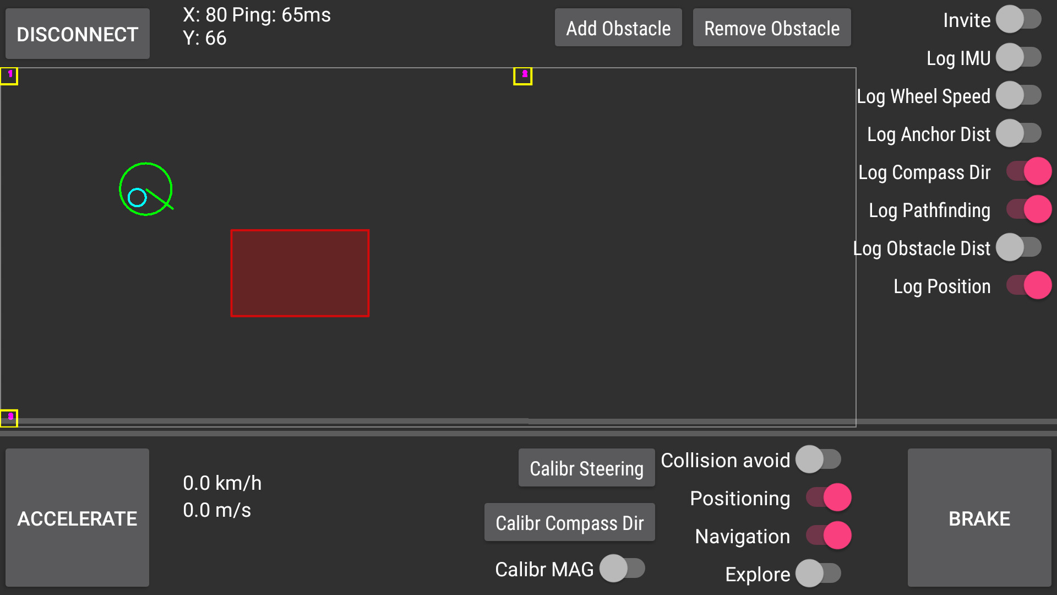
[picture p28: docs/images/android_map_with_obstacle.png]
Map with an obstacle in the Android client


To remove an obstacle, simply select it by tapping on it. The selected obstacle should turn green. Then press the "Remove Obstacle" button.

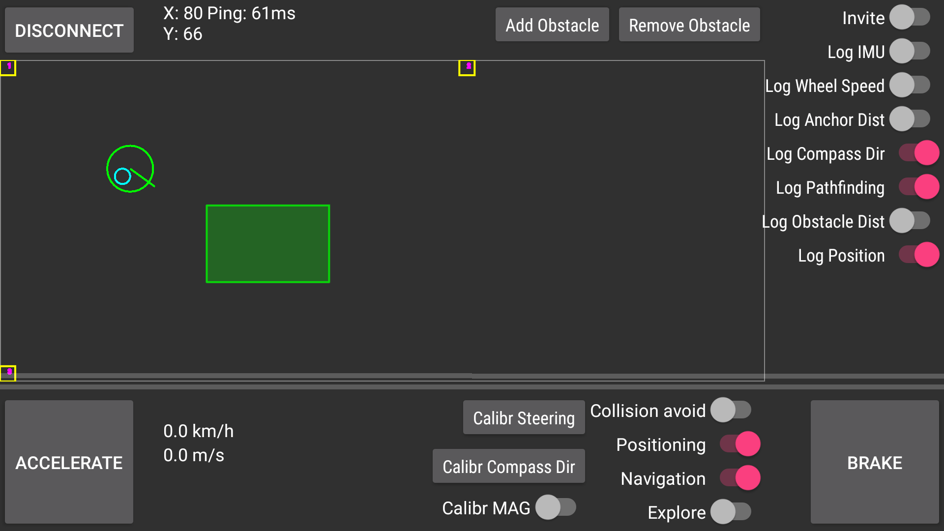
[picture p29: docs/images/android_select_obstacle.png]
Selecting an obstacle in the Android client


## Obstacle detection

Enabling the "Log Obstacle Dist" switch makes the Alphabot start scanning its surroundings for obstacles, if this is not already enabled by the "Collision avoid" or "Explore" switches. The measured obstacle distances are represented visually on the map.

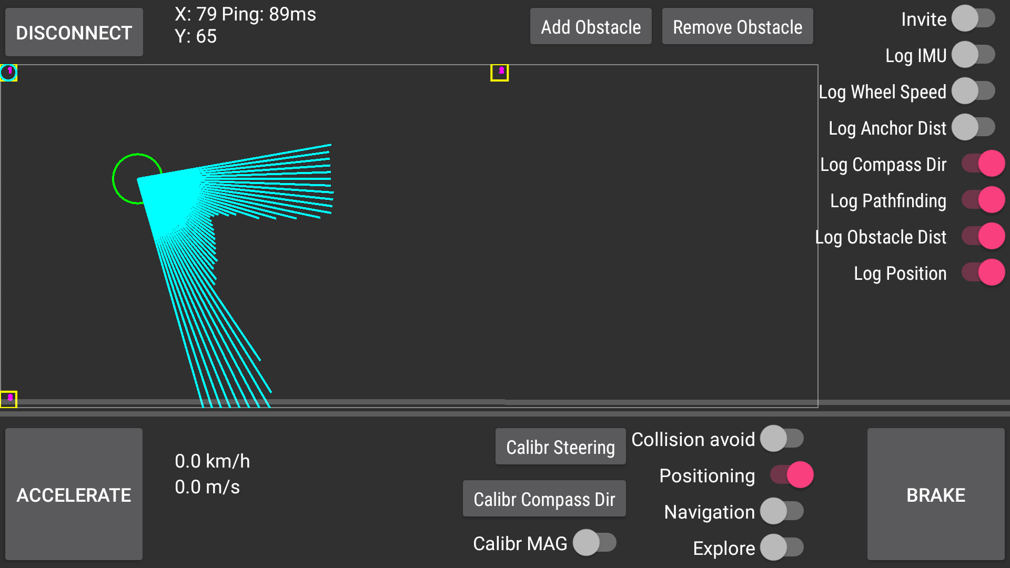
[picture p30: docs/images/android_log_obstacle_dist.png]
Show the obstacle distances in the Android client


## Invite

Enabling the "Invite" switch allows another client to connect to the Alphabot. This way multiple clients can be connected to the Alphabot simultaneously. As soon as another client connects, the "Invite" switch automatically turns off again.

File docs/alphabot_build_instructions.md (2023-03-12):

# Alphabot Build Instructions

First of all, the Alphabot repository is needed. This can be cloned from GitHub with with the following command:

```console
git clone --recursive https://github.com/Filiprogrammer/AlphabotSZUCar.git
```

The ```--recursive``` option ensures that all submodules are cloned as well.

## Parts list

| Part | Amount |
|---|---|
| TT DC Gearbox Motor | 2x |
| DIN 912 M3x10 screw | 9x |
| 28BYJ-48 stepper motor | 2x |
| DIN 912 M3x5 screw | 2x |
| Ball bearing 10x15x4 | 4x |
| Ball bearing 5x11x4 | 4x |
| Ball bearing 5x8x2.5 | 2x |
| DIN 912 M3x14 screw | 4x |
| TF-Luna LiDAR sensor | 1x |
| M2x6 screw | 10x |
| 3S 18650 battery holder case box (7.6x6x2cm) | 1x |
| M2.5x5 screw | 2x |
| 18650 Lithium-Ion Battery 3.7V | 3x |
| DIN 912 M3x8 screw | 2x |
| DIN 912 M3x6 screw | 2x |
| L298N DC motor driver module | 1x |
| M2 screw | 4x |
| M2 male-female hex spacer | 4x |
| M2 nut | 8x |
| M2.5 screw | 6x |
| M2.5 male-female hex spacer | 4x |
| ESP-WROOM-32 board | 1x |
| Arduino Pro Mini 16MHz 5V | 4x |
| USB to TTL adapter (e.g. FT232RL) | 1x |
| 15mm*21mm 2 pins rocker switch | 1x |
| CZM5/2 terminal block | 1x |
| 2.54mm female 12 pin header | 8x |
| 2.54mm female 19 pin header | 2x |
| 2.54mm any 6 pin header | 3x |
| 2.54mm any 4 pin header | 1x |
| S5B-XH-A connector header | 2x |
| DIN 912 M3x5 screw | 6x |
| wire | 16x |
| FC-03 infrared sensor | 2x |

## Custom PCBs to produce

| PCB | Amount |
|---|---|
| pcb/dwm1000_adapter | 4x |
| pcb/alphabot_esp32_pcb | 1x |

## Parts to 3D print

| Part | Amount | Material |
|---|---|---|
| stl/dwm1000.anchor.adapter.board.mount.stl | 3x | PLA |
| stl/vehicle/base/alphabot.4Wheel.base.Top.esp32.stl | 1x | PLA |
| stl/vehicle/base/alphabot.4Wheel.base.suspension.V6.stl | 1x | PLA |
| stl/vehicle/base/frontwheel.suspension.distance.stl | 3x | PLA |
| stl/vehicle/steering/steering.axle.stl | 1x | PLA |
| stl/vehicle/steering/steering.stepper.pin.stl | 1x | PLA |
| stl/vehicle/steering/suspension.left.V4.stl | 1x | PLA |
| stl/vehicle/steering/suspension.right.V4.stl | 1x | PLA |
| stl/vehicle/wheel/rim.front.62mm.V2.stl | 2x | PLA |
| stl/vehicle/wheel/rim.back.62mm.V2.stl | 2x | PLA |
| stl/vehicle/wheel/rim.62mm.front.bearing.cage.V2.stl | 2x | PLA |
| stl/vehicle/wheel/rim.62mm.back.bearing.cage.V2.stl | 2x | PLA |
| stl/vehicle/wheel/rim.62mm.front.nut.stl | 4x | PLA |
| stl/vehicle/wheel/tire.base.62.78.stl | 4x | Filaflex |
| stl/vehicle/wheel/rim.axle.back.stl | 2x | PLA |
| stl/vehicle/addon/wingv4.stl | 1x | PLA |
| stl/vehicle/addon/wing.holder.V4.hc-sr04.stl | 1x | PLA |
| stl/vehicle/addon/dwm1000.tag.adapter.board.mount.stl | 1x | PLA |
| stl/vehicle/addon/bumper.lidar.holder.stl | 1x | PLA |
| stl/vehicle/addon/bumper.lidar.front.stl | 1x | PLA |
| stl/vehicle/addon/wheel.encoder.stl | 2x | PLA |

## Positioning module

### Assembly

After ordering the DWM1000 adapter PCB with assembly service, the board should look like this:

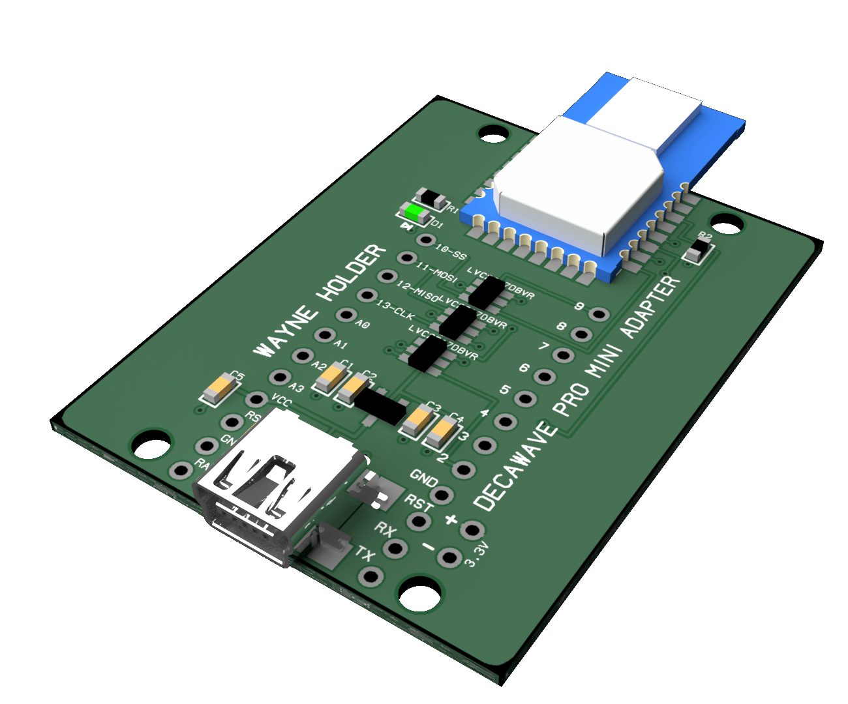
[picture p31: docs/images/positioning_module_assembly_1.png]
Positioning module assembly 1


Now solder pin headers for the Arduino Pro Mini to the board as seen in the following picture.

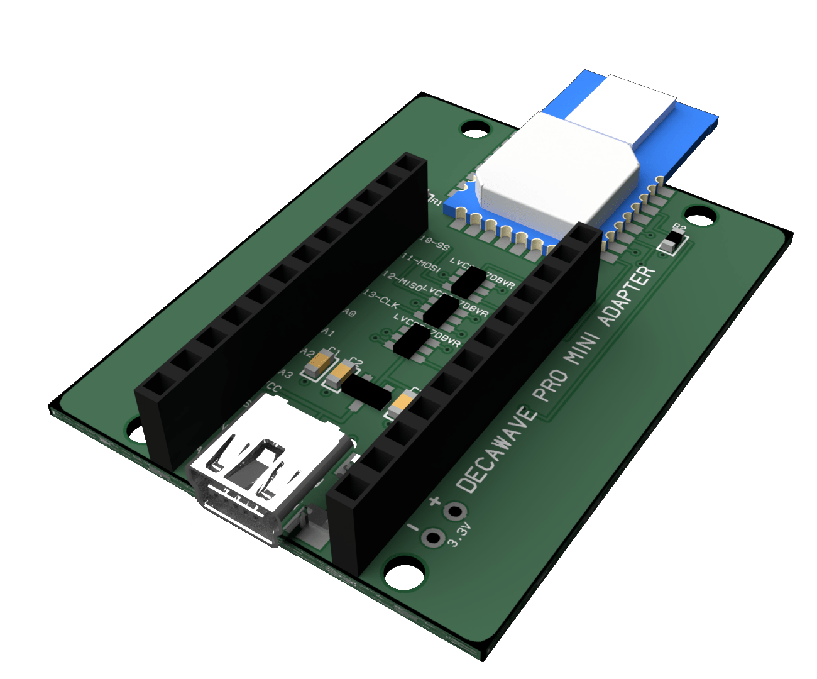
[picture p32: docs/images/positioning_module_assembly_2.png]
Positioning module assembly 2


Finally plug the Arduino Pro Mini into the DWM1000 Adapter.

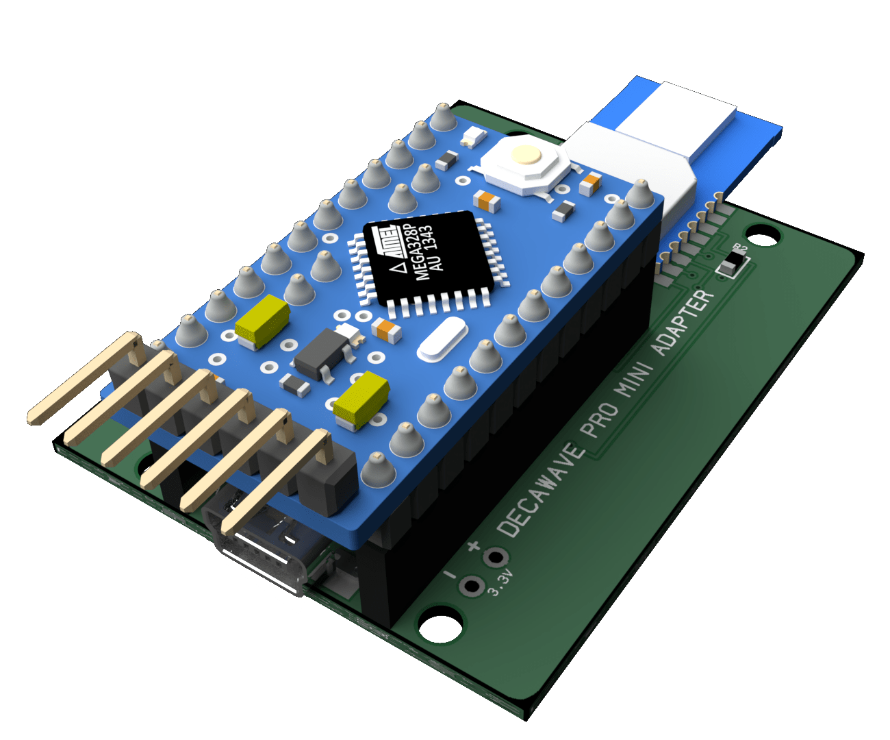
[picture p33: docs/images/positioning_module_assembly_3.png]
Positioning module assembly 3


### Software

The software for the microcontrollers can be built with PlatformIO. PlatformIO is a useful tool for development for various embedded systems. This tool can be used either standalone or as an extension in Visual Studio Code. The process with this Visual Studio Code extension is explained below.

To install the extension, click on the Extensions tab in Visual Studio Code and search for PlatformIO.

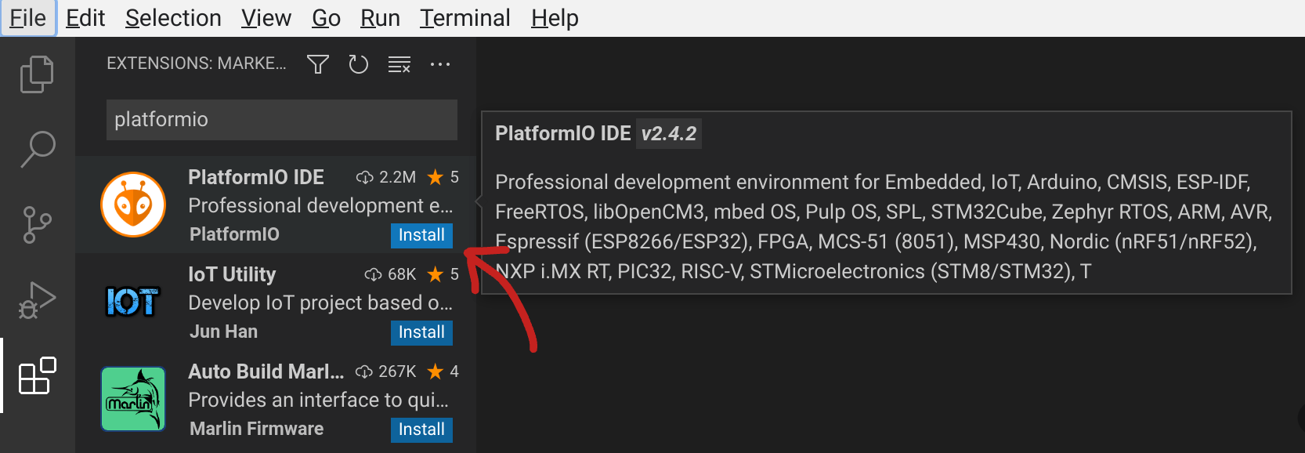
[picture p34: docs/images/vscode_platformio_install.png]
Installing PlatformIO in VSCode


Click "Install" to install the extension. Restart Visual Studio Code once the installation has completed.

For the positioning system, the Arduino Pro Mini, which acts as a "tag" on the Alphabot, must be flashed with the appropriate firmware. Open the positioning_tag folder of the Alphabot repository in VSCode. The Arduino Pro Mini has to be connected to the computer with a USB to TTL adapter like the FT232RL.

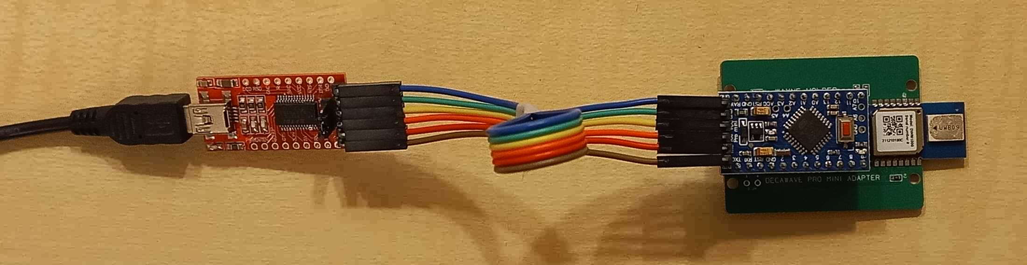
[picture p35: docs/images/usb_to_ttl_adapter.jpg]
Aduino Pro Mini connected through USB to TTL adapter


The firmware can be uploaded to the Arduino Pro Mini by clicking the upload button in VSCode.

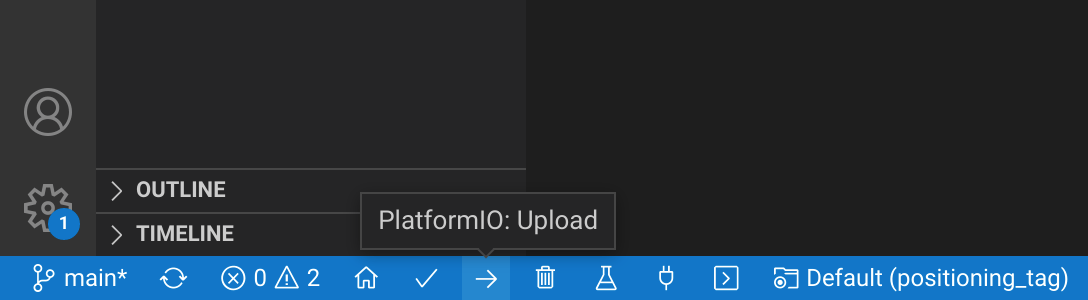
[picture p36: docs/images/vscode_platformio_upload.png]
VSCode PlatformIO upload


Now the firmware is built and uploaded to the Arduino Pro Mini via the adapter. Once this process completes, check whether it worked by taking a look at the Serial Monitor.

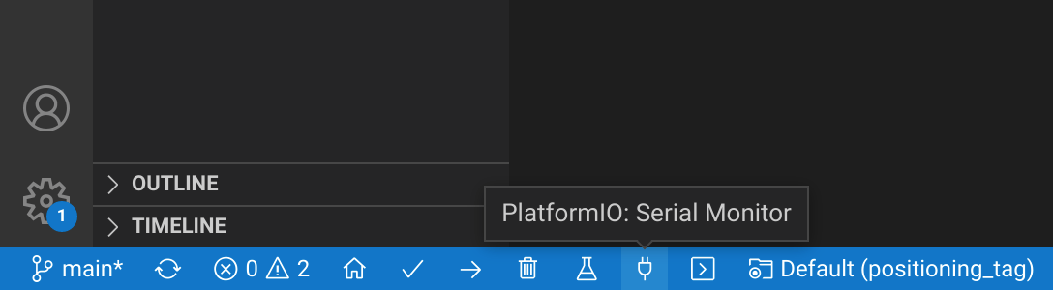
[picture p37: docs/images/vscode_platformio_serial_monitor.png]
VSCode PlatformIO serial monitor


If the process was successful, the following message will appear in the Serial Monitor:

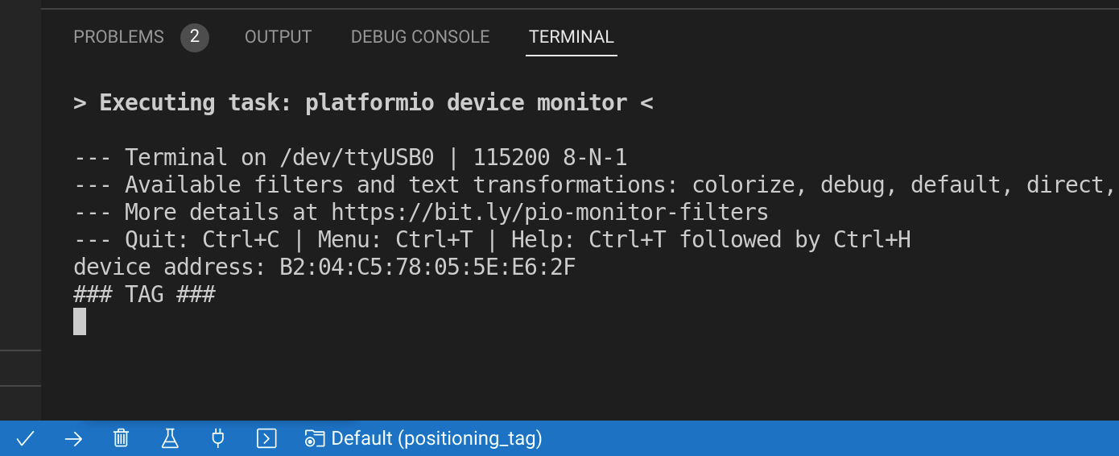
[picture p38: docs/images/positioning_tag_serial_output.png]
Serial output of positioning tag


Next, the anchors can be set up. Plug an Arduino Pro Mini that is to be used as an anchor into the adapter. Open the folder positioning_anchor of the Alphabot repository in VSCode.

Now go to line 27 of positioning_anchor/DWM1000_Anchor/DWM1000_Anchor.ino.

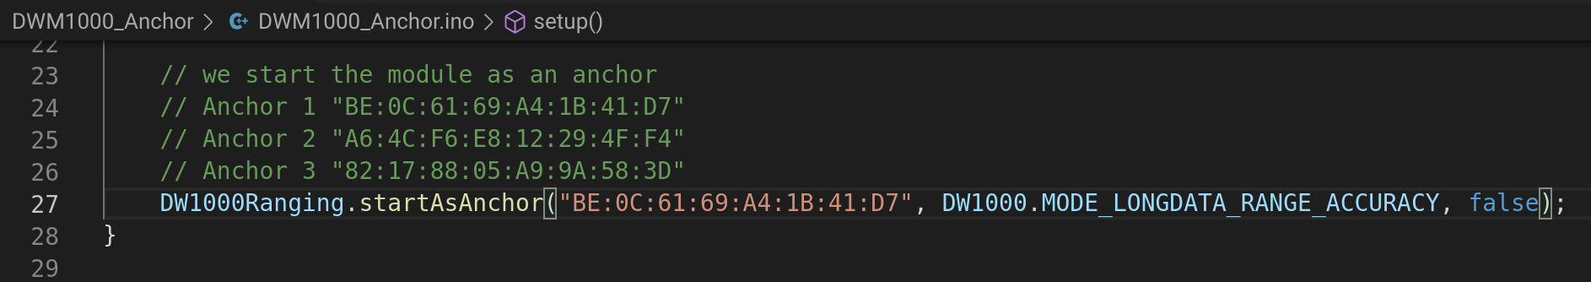
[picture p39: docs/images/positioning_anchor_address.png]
Positioning anchor address


Each anchor should have its own address. The addresses from the comments on lines 24 to 26 are to be used when uploading. For clarity, it is helpful to label the positioning modules accordingly.

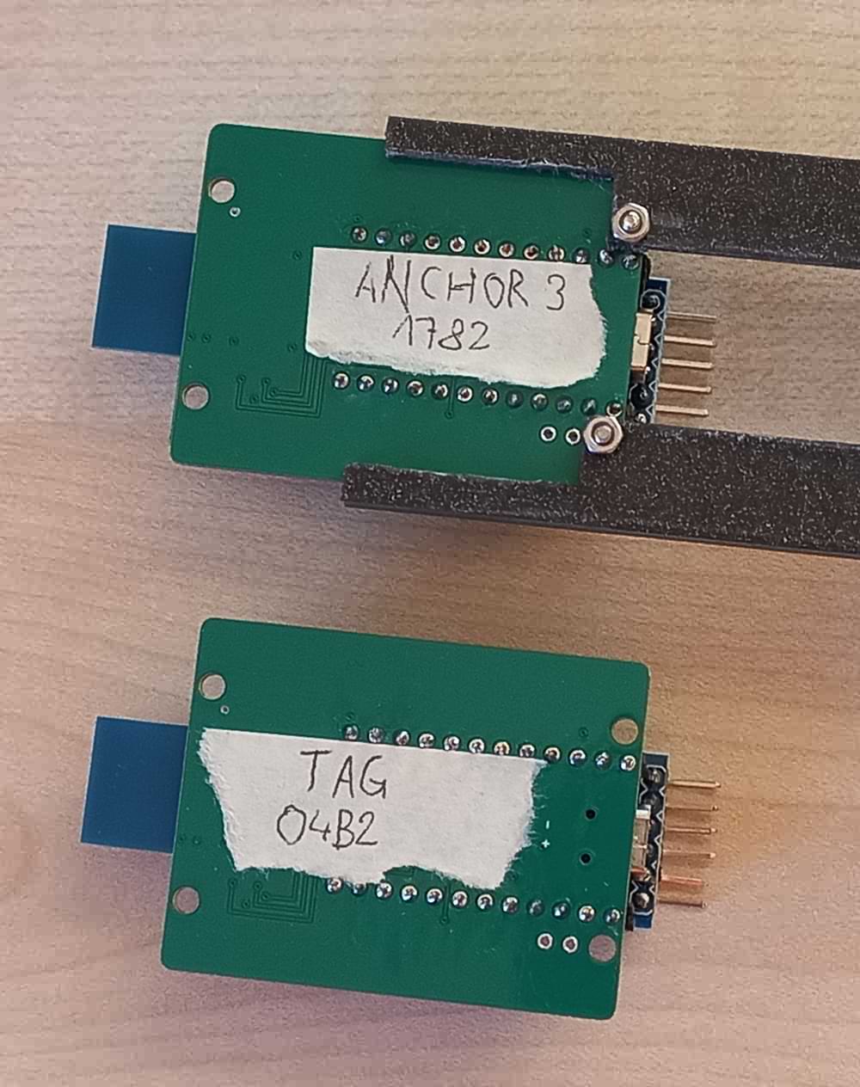
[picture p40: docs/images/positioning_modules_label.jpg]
Labeled positioning modules


Once the firmware is uploaded, the serial monitor should display the following message with the corresponding address:

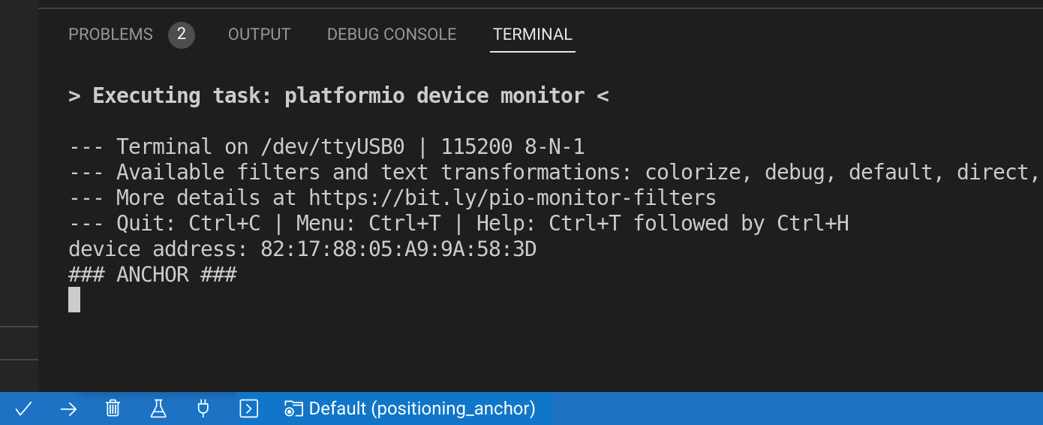
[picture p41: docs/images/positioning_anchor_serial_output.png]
Serial output of positioning anchor


Upload the firmware to the other two anchors as well. Always make sure that the correct address is entered on line 27 before uploading.

If everything went well, all anchors will connect to the tag when the positioning modules are connected to the power. Each Arduino Pro Mini should write the measured distances to the serial interface.

### Attaching an anchor to a holder

Insert a positioning module configured as an anchor into an anchor holder (stl/dwm1000.anchor.adapter.board.mount.stl)

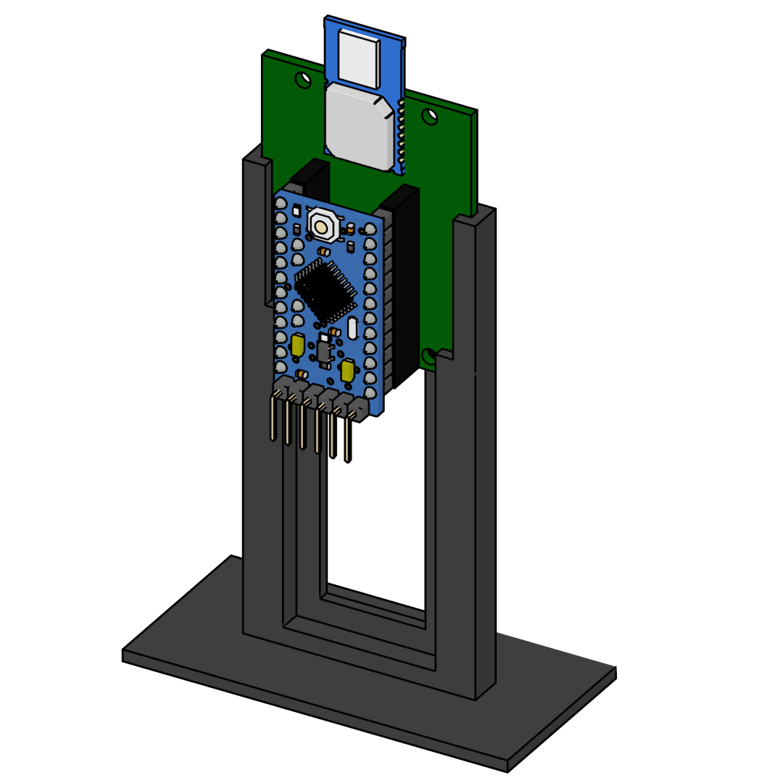
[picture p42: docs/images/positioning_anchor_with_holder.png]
Positioning anchor with a holder


Screw the positioning module on with two M2x6 screws and two M2 nuts.

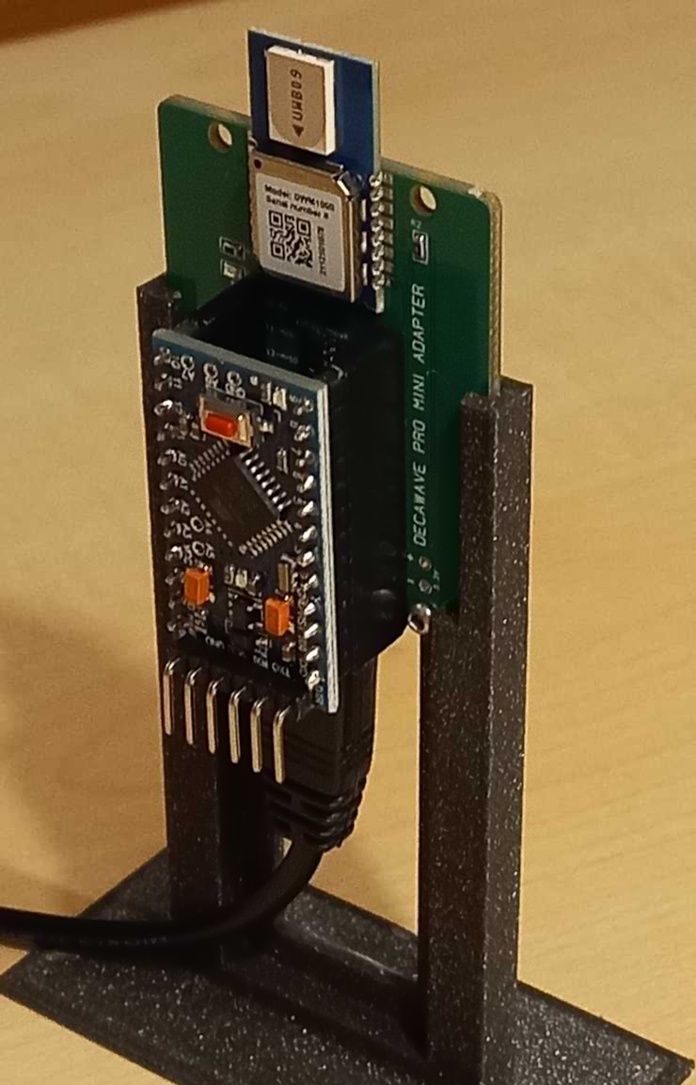
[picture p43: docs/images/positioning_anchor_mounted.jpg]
Positioning anchor mounted to a holder


Repeat this process for the other two anchors.

## Alphabot ESP32 PCB assembly

After ordering the Alphabot ESP32 PCB with assembly service, the board should look like this:

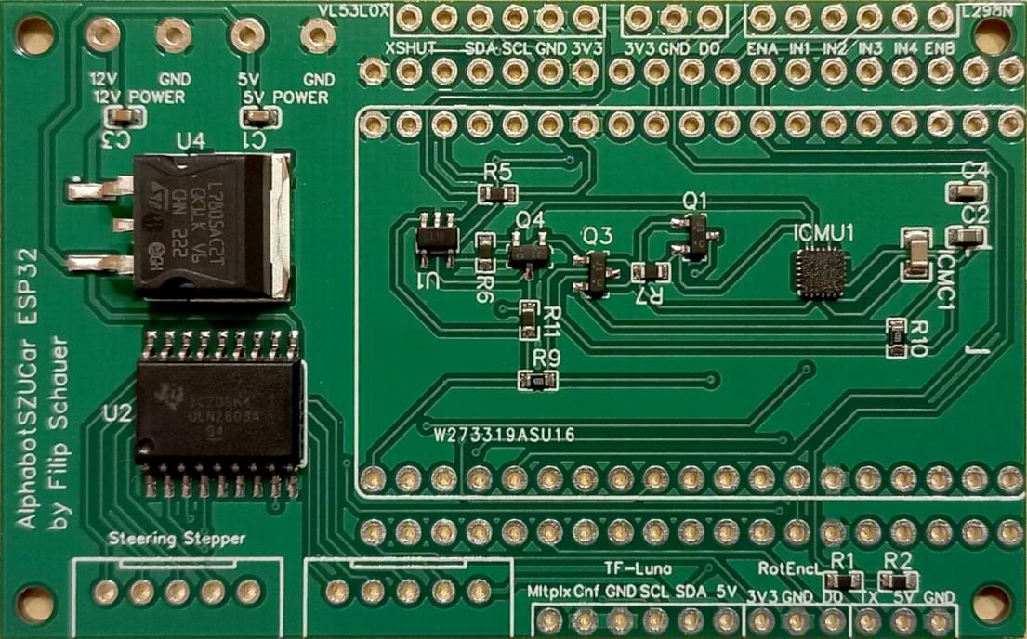
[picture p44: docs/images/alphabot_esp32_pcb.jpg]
Alphabot ESP32 PCB


Now solder the pin headers for the ESP-WROOM-32, for the L298N motor driver, for the positioning module, for the TF-Luna LiDAR sensor and for the wheel encoders to the board.

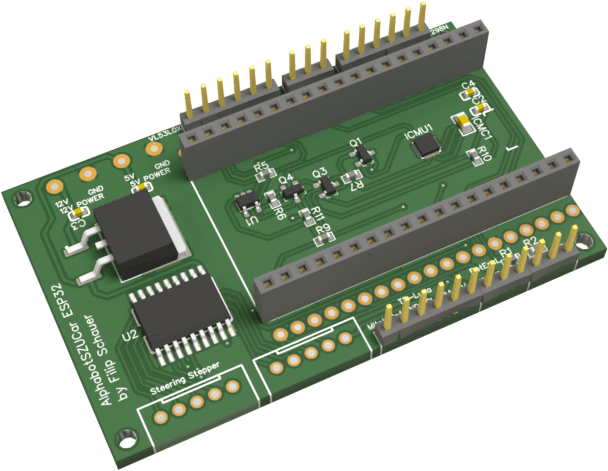
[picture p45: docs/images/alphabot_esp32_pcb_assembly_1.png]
Alphabot ESP32 PCB assembly 1


Also solder two S5B-XH-A connector headers for the stepper motors to the board as seen in the following picture.

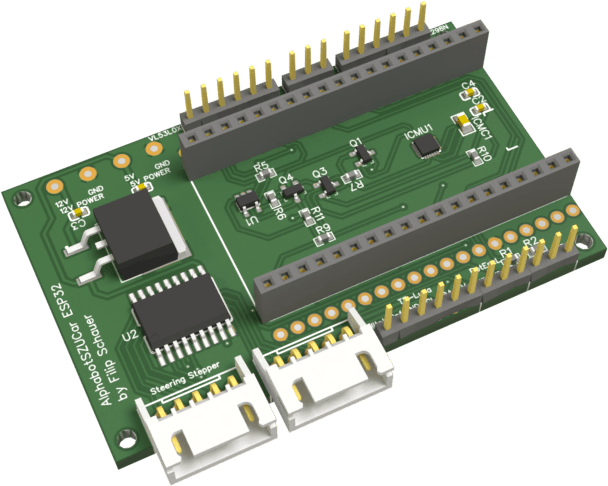
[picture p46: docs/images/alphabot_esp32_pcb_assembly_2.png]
Alphabot ESP32 PCB assembly 2


Solder a CZM5/2 terminal block to the 12V power pins of the board.

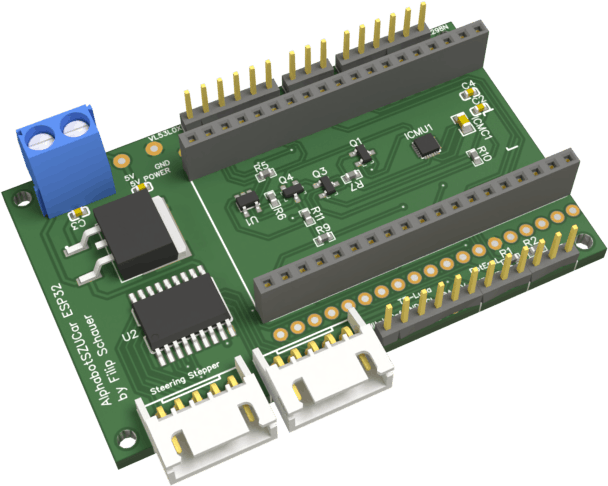
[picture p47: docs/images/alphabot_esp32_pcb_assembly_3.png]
Alphabot ESP32 PCB assembly 3


Finally you can plug the ESP-WROOM-32 into the Alphabot ESP32 PCB.

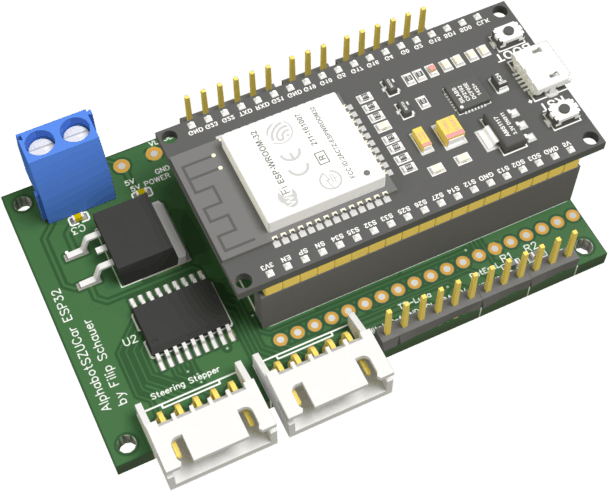
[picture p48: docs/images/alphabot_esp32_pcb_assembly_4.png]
Alphabot ESP32 PCB assembly 4


## Alphabot car assembly

Start with soldering the gear motors. Both contacts of the motor are to be soldered to a separate wire.

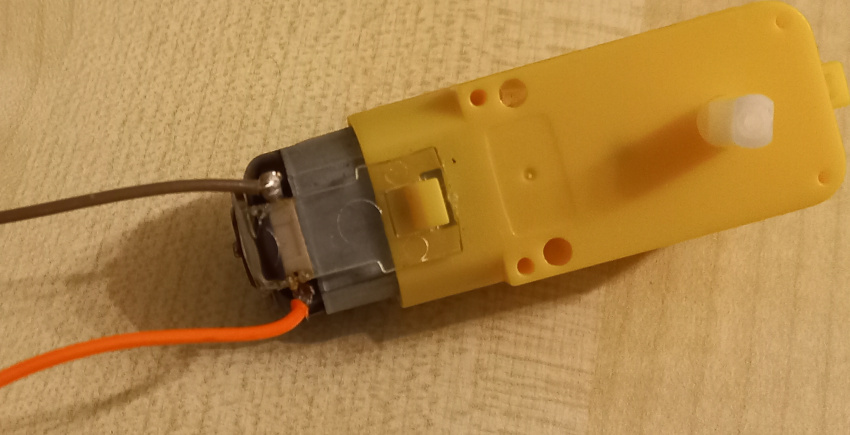
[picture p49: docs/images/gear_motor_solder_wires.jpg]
Solder wires to the contacts of the drive motor


Once the gear motors are soldered, insert them on the bottom of the base plate (stl/vehicle/base/alphabot.4Wheel.base.Top.esp32.stl) of the Alphabot.

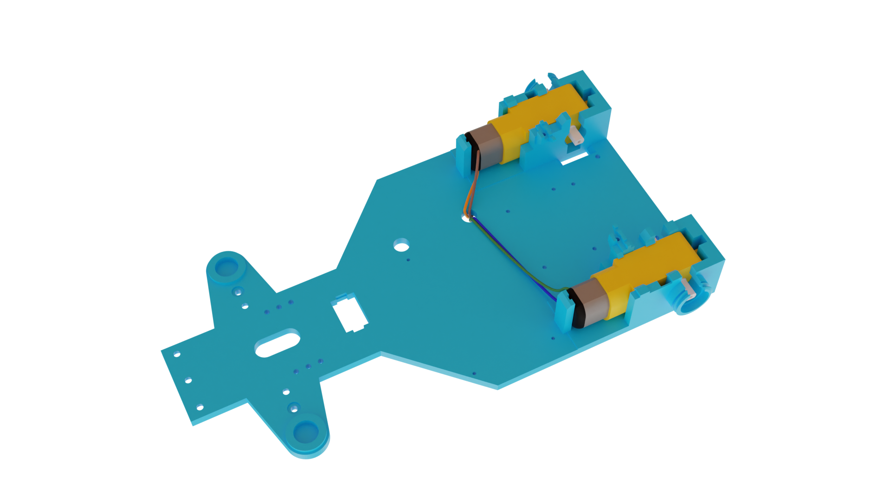
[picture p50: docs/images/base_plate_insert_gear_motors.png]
Insert gear motors into the base plate


Now take the wheel encoders (stl/vehicle/addon/wheel.encoder.stl) and put them onto the hubs of the motors as seen in the pictures below.

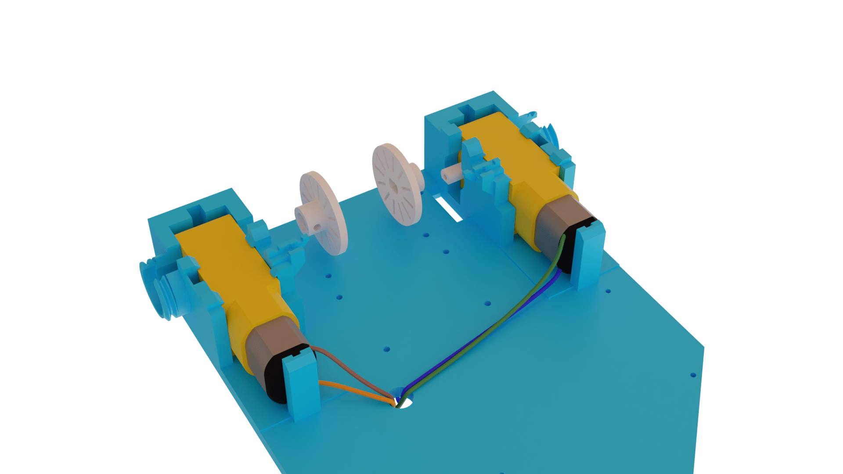
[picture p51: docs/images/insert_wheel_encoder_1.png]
Insert the wheel encoder 1


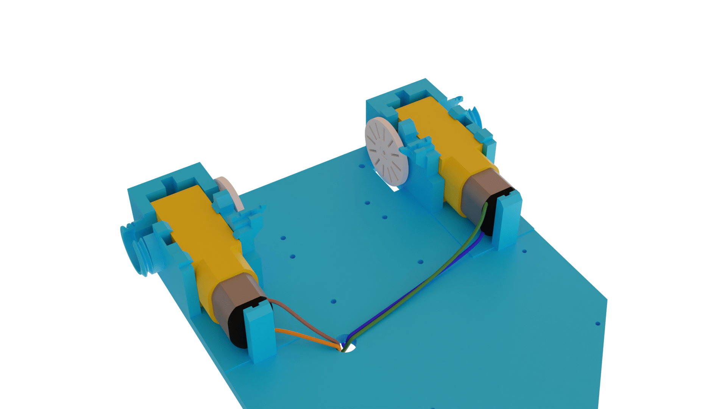
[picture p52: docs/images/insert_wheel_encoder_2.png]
Insert the wheel encoder 2


Next, pull a tire (stl/vehicle/wheel/tire.base.62.78.stl) onto a rear wheel. (stl/vehicle/wheel/rim.back.62mm.V2.stl)

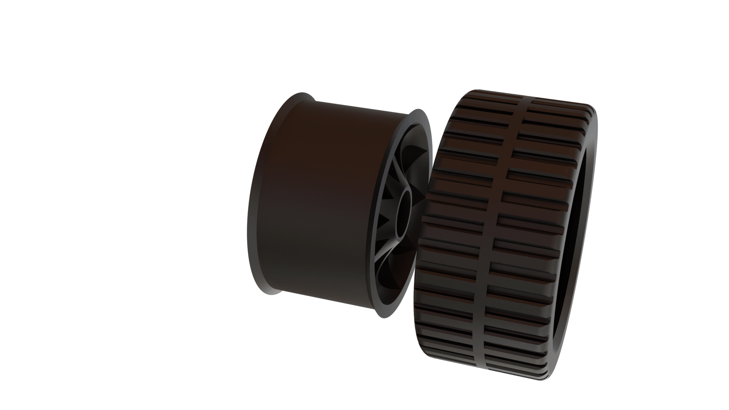
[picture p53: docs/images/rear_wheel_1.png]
Pull a tire onto a rear wheel


This results in a ready rear wheel.

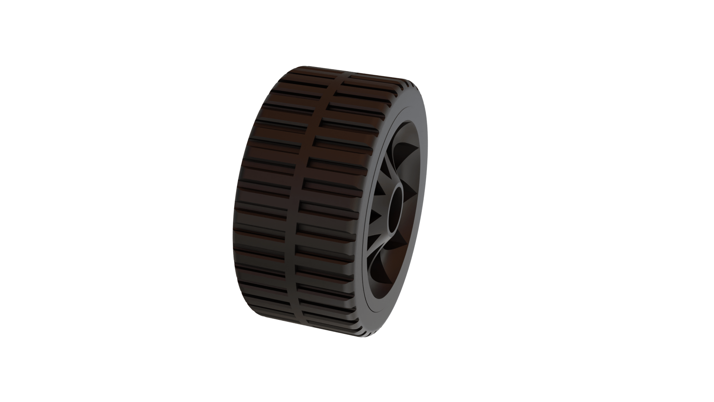
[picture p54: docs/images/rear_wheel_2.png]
Rear wheel with tire


Attach a rear wheel to the gear motor on each side.

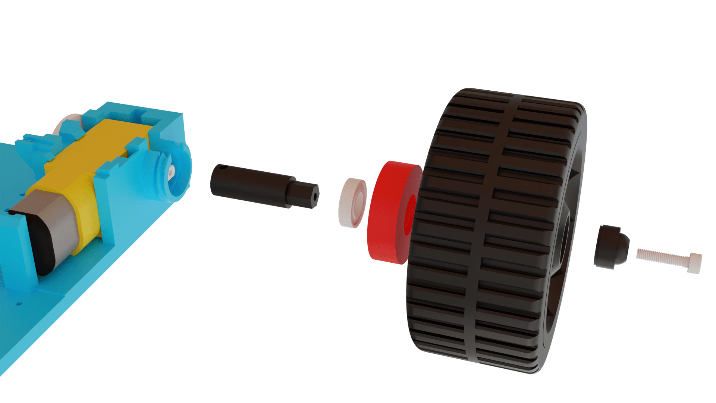
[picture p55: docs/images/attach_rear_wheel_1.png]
Attach a rear wheel 1


When mounting the rear wheel, first attach the axle (stl/vehicle/wheel/rim.axle.back.stl) to the motor hub.

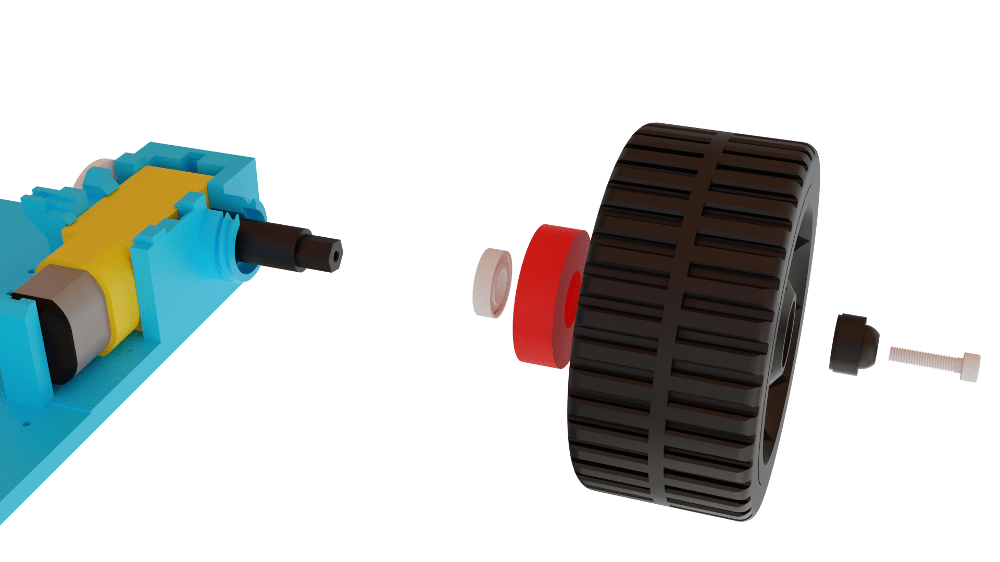
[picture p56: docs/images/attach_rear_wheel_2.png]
Attach a rear wheel 2


For a stable position of the wheel axle, slide a 10x15x4 ball bearing around the wheel axle, so that the motor can still easily turn the wheel.

Attach a rear wheel 3

To prevent the ball bearing from falling out, screw a wheel axle cover (stl/vehicle/wheel/rim.62mm.back.bearing.cage.V2.stl) onto it.

Attach a rear wheel 4

Attach the rear wheel to the axle.

Attach a rear wheel 5

Screw the wheel to the axle with a wheel nut (stl/vehicle/wheel/rim.62mm.front.nut.stl) and a DIN 912 M3x14 screw so that the wheel is securely mounted on the axle.

Attach a rear wheel 6

Once both rear wheels are attached it should look like this:

Rear wheels are attached

Next, the base plate with the motors can be put aside for the time being. Screw three spacers (stl/vehicle/base/frontwheel.suspension.distance.stl) to the steering bracket (stl/vehicle/base/alphabot.4Wheel.base.suspension.V6.stl) using three DIN 912 M3x10 screws.

Steering bracket 1

Steering bracket 2

Now screw a 28BYJ-48 stepper motor to the front bumper (stl/vehicle/addon/bumper.lidar.front.stl) using two DIN 912 M3x10 screws.

Front bumper 1

Attach the LiDAR holder (stl/vehicle/addon/bumper.lidar.holder.stl) to the hub of the stepper motor.

Front bumper 2

In the next step, screw the steering bracket to the front bumper. Use four DIN 912 M3x5 screws for this.

Screw the steering bracket to the front bumper 1

Screw the steering bracket to the front bumper 2

In the next step, return to the base plate. Attach a stepper motor for steering to the base plate using two DIN 912 M3x5 screws.

Attach a steering stepper motor to the base plate 1

Attach a steering stepper motor to the base plate 2

Once the stepper motor has been screwed to the base plate, the steering extension (stl/vehicle/steering/steering.stepper.pin.stl) can be attached to the the stepper motor hub protruding from the bottom of the base plate.

Attach the steering extension

Now insert the two 5x8x2.5 ball bearings on the steering axle (stl/vehicle/steering/steering.axle.stl).

Insert ball bearings on the steering axle

Attach the steering axle to the steering extension with a DIN 912 M3x10 screw. Insert 5x11x4 ball bearings in the provided recesses and place the steering suspensions (stl/vehicle/steering/suspension.left.V4.stl & stl/vehicle/steering/suspension.right.V4.stl) on top.

Attach the steering axle & suspenions 1

Attach the steering axle & suspenions 2

Attach 5x11x4 ball bearings to the underside of the steering axles.

Attach the steering axle & suspenions 3

Now the two large parts can be screwed together. Screw the spacers to the base plate using three DIN 912 M3x10 screws. The ball bearings should fit into the provided recesses.

Screw base plate and steering bracket together 1

Screw base plate and steering bracket together 2

The next step is to mount the front wheels.

Attach a front wheel 1

First slide the front bearing cage (stl/vehicle/wheel/rim.62mm.front.bearing.cage.V2.stl) containing a 10x15x4 ball bearing onto the front wheel axle.

Attach a front wheel 2

Slide the front wheel (stl/vehicle/wheel/rim.front.62mm.V2.stl & stl/vehicle/wheel/tire.base.62.78.stl) onto the axle and screw the bearing cage onto the inside of the wheel.

Attach a front wheel 3

Then screw the wheel to the axle with a wheel nut (stl/vehicle/wheel/rim.62mm.front.nut.stl) and a DIN 912 M3x14 screw so that it does not come loose while driving.

Attach a front wheel 4

For obstacle detection, screw the TF-Luna LiDAR sensor to the dedicated holder at the front. Use M2x6 screws for that.

Attach the TF-Luna LiDAR sensor 1

Attach the TF-Luna LiDAR sensor 2

Insert a 15mm*21mm 2 pins rocker switch through the base plate at the designated location.

Insert the rocker switch

The battery case can be screwed to the underside of the base plate with two M2.5x5mm screws. Furthermore, interrupt a power line from the battery case with the rocker switch.

Battery case on the underside of the base plate

Mount an FC-03 infrared sensor around the encoder wheel with an M2.5 screw. Do the same thing around the other encoder wheel.

FC-03 infrared sensor

Screw four M2 hex spacers into the screw holes provided for the Alphabot ESP32 PCB and screw four M2.5 hex spacers into the screw holes provided for the L298N.

Hex spacers

Up next, mount the rear spoiler to the rear of the base plate. Mount the wing holder (stl/vehicle/addon/wing.holder.V4.hc-sr04.stl) to the base plate with two DIN 912 M3x8 screws and mount the wing (stl/vehicle/addon/wingv4.stl) to the wing holder with two DIN 912 M3x6 screws.

Mount the wing

For the positioning module, attach the holder for the tag (stl/vehicle/addon/dwm1000.tag.adapter.board.mount.stl) to the base plate.

Attach the tag holder to the base plate

Screw the L298N motor driver to the base plate with M2.5 screws and connect it to the drive motors and the power supply.

L298N motor driver

Now the heart of this Alphabot comes into play: the Alphabot ESP32 PCB. Attach the Alphabot ESP32 PCB with the ESP-WROOM-32 plugged in to the base plate using M2 male-female hex spacers and M2 screws.

Attach the Alphabot ESP32 PCB

Connect the Alphabot ESP32 PCB to the power supply through its 12V power connectors.

Connect the Alphabot ESP32 PCB to 12V power

Connect the pins of the L298N motor driver to the Alphabot ESP32 PCB.

Connect L298N to Alphabot ESP32 PCB

Now insert the positioning module configured as a tag into the DWM1000 tag holder.

Insert the positioning tag into the tag holder

Connect the GND, VCC and TXO pins on the Arduino Pro Mini of the positioning module to the Alphabot ESP32 PCB.

Connect Arduino Pro Mini pins to the Alphabot ESP32 PCB

Screw the positioning module on with two M2x6 screws and two M2 nuts.

Screw the positioning tag on

Connect the steering stepper motor to the correspondingly labeled B5B-XH-AM connector header on the Alphabot ESP32 PCB.

Connect the steering stepper motor to the Alphabot ESP32 PCB

Connect the stepper motor at the front to the other B5B-XH-AM connector header on the Alphabot ESP32 PCB.

Connect the front stepper motor to the Alphabot ESP32 PCB

Connect the TF-Luna LiDAR sensor at the front to the Alphabot ESP32 PCB.

Connect the TF-Luna to the Alphabot ESP32 PCB

Connect the FC-03 wheel encoder sensors to the Alphabot ESP32 PCB via the VCC, GND and D0 pins.

Connect the FC-03 sensors to the Alphabot ESP32 PCB 1

Connect the FC-03 sensors to the Alphabot ESP32 PCB 2

Now that the Alphabot is successfully assembled, the software part can begin.

Assembled Alphabot

## ESP32 Software

Open the directory esp32 in VSCode. Make sure that the Alphabot's power is turned off and connect the ESP32 to the computer. The firmware can be uploaded to the ESP32 by clicking the Upload button in VSCode.

Alternatively this can also be done via the command line:

```console
pio run --target upload
```

If the upload process was successful, the ESP32 will now execute the uploaded code. The ESP32 can be unplugged from the computer and be used in real operation.

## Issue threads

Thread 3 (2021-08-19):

Design Alphabot ESP32 PCB

Filiprogrammer, 2021-08-19:
Replace most of the wiring of the ESP32 version with a PCB to make it more manageable and avoid loose connections.

Closed 2021-12-08.

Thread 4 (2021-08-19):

Implement VL53L0X ranging sensor on ESP32

Filiprogrammer, 2021-08-19:
Implement the VL53L0X infrared time-of-flight ranging sensor on the ESP32 version as an alternative to the HC-SR04 ultrasonic ranging sensor. The VL53L0X should yield more accurate results with the downside of not working properly in sunlight.

To achieve this on the ESP32 version, we might have to rethink the I2C topology.

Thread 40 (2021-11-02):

Create TCP Test server and client

LecraM2003, 2021-11-02:
Create a client and a server for testing the tcp client library

LecraM2003, 2021-11-02:
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
Implemented but waiting for merging old things

LecraM2003, 2021-11-02:
#duration: 2

LecraM2003, 2021-11-16:
> 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 Implemented but waiting for merging old things

This was changed to the following example, because the distance sensor request doesnt exist anymore
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

Closed 2021-12-07.

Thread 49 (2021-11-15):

Refactor Alphabot.NET with present functionality

LecraM2003, 2021-11-15:
Refactor the following things:

- [x] Alphabot Actions
- [x] Add Requests and Responses
- [x] Speed, Steer, Calibrate, Ping and Collision Avoidance should be possible

Closed 2022-01-03.

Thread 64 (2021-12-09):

Add missing sensors in protocol and client library

LecraM2003, 2021-12-09:
Add:
- gyroscope
- accelerometer
- wheel speed
- anchor distances

DURATION ALREADY: 1h

Closed 2022-01-01.

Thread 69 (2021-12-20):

Implement error responses on Alphabot.NET

LecraM2003, 2021-12-20:
Implement error responses on Alphabot.NET raspberry,
send an error back if the packet is invalid

Closed 2022-01-03.

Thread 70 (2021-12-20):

Add missing sensors on Raspberry Alphabot

LecraM2003, 2021-12-20:
Add following sensors physically, as well as in the Alphabot.NET code:

- compass
- accelerometer
- gyroscope
- unsure? wheel speed sensor
- unsure? lidar sensor

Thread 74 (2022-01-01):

Fix steering problems on Raspberry Pi

LecraM2003, 2022-01-01:
Since the gyroscope control on the client was implemented, there is a problem with the steering. It seems like the steering works relative and not absolute.

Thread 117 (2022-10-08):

Assembling the hardware

Ezward, 2022-10-08:
I would love to build this project, but I don't trust I could reproduce the build.  Any documentation you could provide would be so helpful.  A parts lists of bolt/nut sizes, bearings and other hardware and instructions on how to assemble the steering mechanism would give me info that I need.  Maybe just a image with pointers and part numbers.  Thank you for this project.

Closed 2022-12-18.

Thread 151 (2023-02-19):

Second encoder on Raspberry Pi

Ezward, 2023-02-19:
The Esp32 variant's STL has been updated to include a second encoder on the right wheel.  It would be great to have this same thing on the Raspberry Pi.  We can then get a better estimate of orientation using the two encoders.  We could also implement closed loop speed control for both motors, and using a kinematics model, create a software differential so each back wheel's target velocity is calculated to match that required by the target forward velocity and the wheel's distance from the center of rotation of the turn imparted by the steering angle.

A render or photo of the RaspberryPi build would also be useful so I can adapt the Esp32 build instructions for the RaspberryPi.

Ezward, 2023-02-19:
I'm not much of a 3d modeler; I've attempted do this myself in TinkerCad, but TinkerCad is not up for the job.  Duplicating and mirroring almost work, but all the non-symmetrical holes end up as filled.

Filiprogrammer, 2023-02-21:
I adapted the STL file for the base plate of the Raspberry Pi variant.
Since I don't have and never had an assembled Raspberry Pi build of the Alphabot, I won't write build instructions for it. I only ever had a physical version of the ESP32 variation, as it is much more efficient to use the ESP32 for this project. (In terms of power consumption and complexity) The code for the Raspberry Pi variant is also far behind and barely supports any features of the ESP32 variant. It's fair to say that the Raspberry Pi variation is no longer maintained.

Ezward, 2023-07-25:
@Filiprogrammer thank you.  I'll print this out and give it a try.  I plan to implement the software differential and adapt [DonkeyCar](https://github.com/autorope/donkeycar) to run on it.

Closed 2023-02-24.

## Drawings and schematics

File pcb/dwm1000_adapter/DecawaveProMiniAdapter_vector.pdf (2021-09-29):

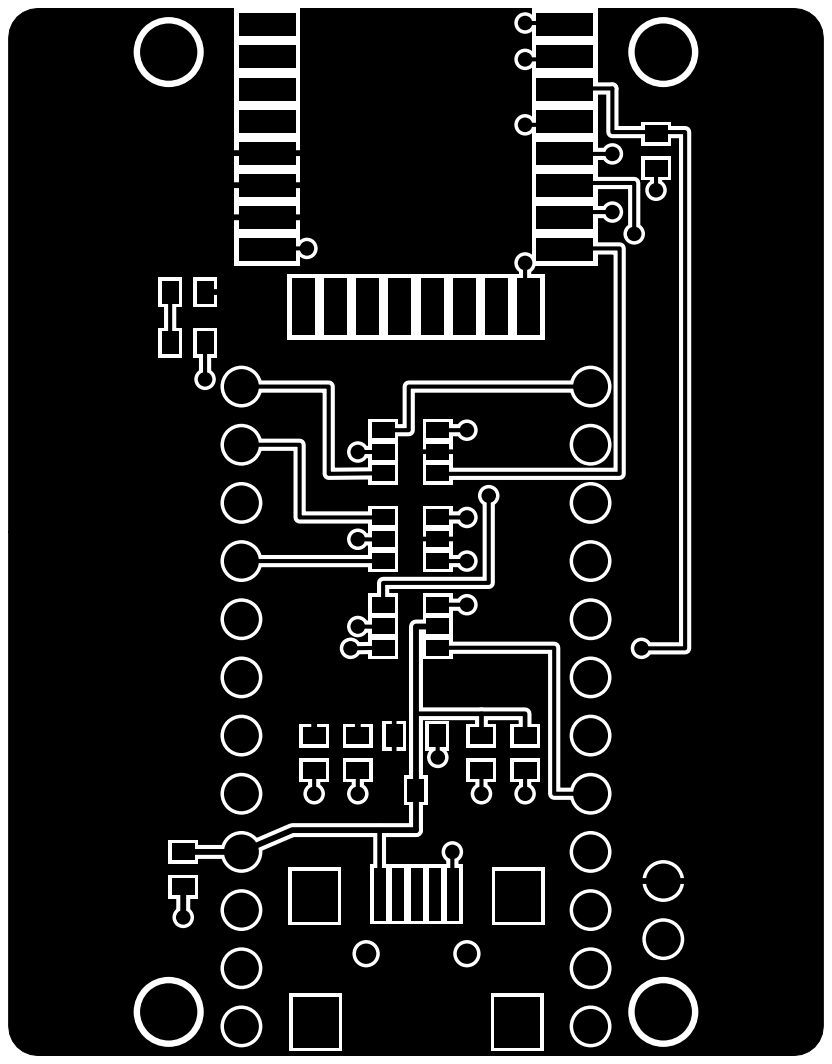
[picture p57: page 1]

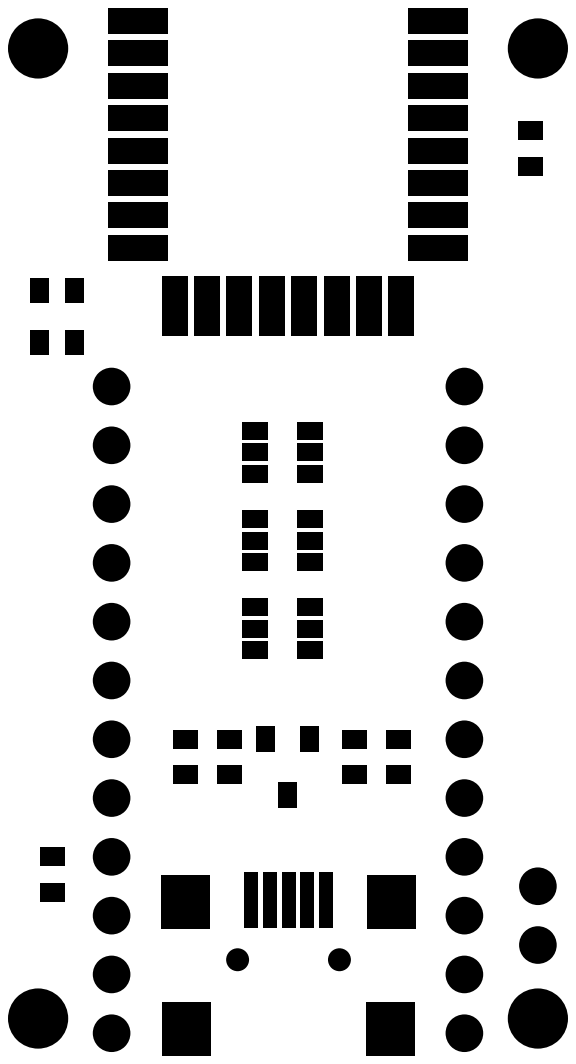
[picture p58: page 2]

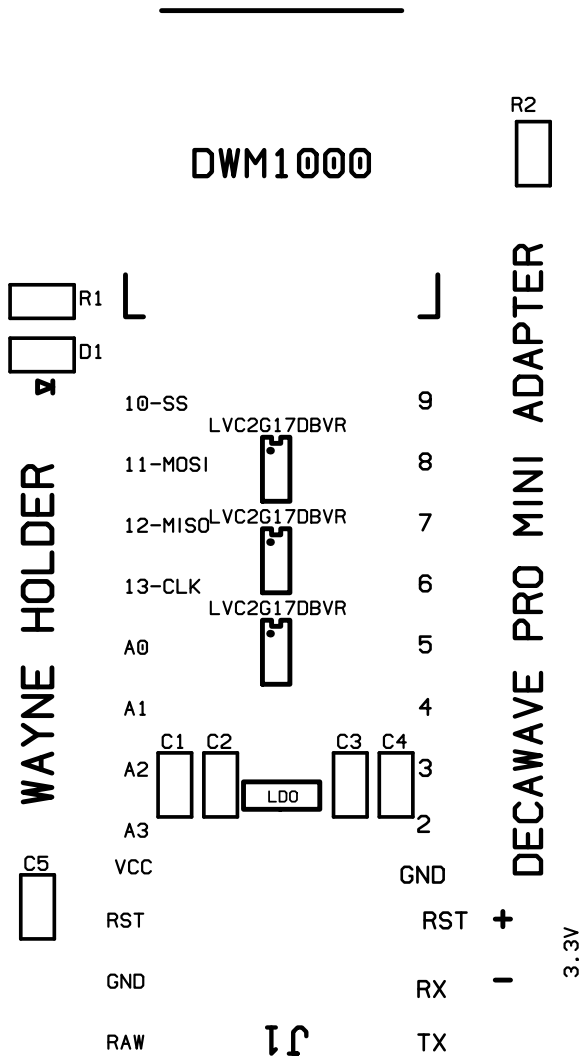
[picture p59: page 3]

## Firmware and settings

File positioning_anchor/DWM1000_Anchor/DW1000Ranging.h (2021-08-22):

/*
 * Copyright (c) 2015 by Thomas Trojer <thomas@trojer.net> and Leopold Sayous <leosayous@gmail.com>
 * Decawave DW1000 library for arduino.
 *
 * Licensed under the Apache License, Version 2.0 (the "License");
 * you may not use this file except in compliance with the License.
 * You may obtain a copy of the License at
 *
 *     http://www.apache.org/licenses/LICENSE-2.0
 *
 * Unless required by applicable law or agreed to in writing, software
 * distributed under the License is distributed on an "AS IS" BASIS,
 * WITHOUT WARRANTIES OR CONDITIONS OF ANY KIND, either express or implied.
 * See the License for the specific language governing permissions and
 * limitations under the License.
 *
 * @file DW1000Ranging.h
 * Arduino global library (header file) working with the DW1000 library
 * for the Decawave DW1000 UWB transceiver IC.
 *
 * @TODO
 * - remove or debugmode for Serial.print
 * - move strings to flash to reduce ram usage
 * - do not safe duplicate of pin settings
 * - maybe other object structure
 * - use enums instead of preprocessor constants
 */

#ifndef _DW1000Ranging_H_INCLUDED
#define _DW1000Ranging_H_INCLUDED

#include "DW1000.h"
#include "DW1000Time.h"
#include "DW1000Device.h" 
#include "DW1000Mac.h"

// messages used in the ranging protocol
#define POLL 0
#define POLL_ACK 1
#define RANGE 2
#define RANGE_REPORT 3
#define RANGE_FAILED 255
#define BLINK 4
#define RANGING_INIT 5

#define LEN_DATA 90

//Max devices we put in the networkDevices array ! Each DW1000Device is 74 Bytes in SRAM memory for now.
#define MAX_DEVICES 4

//Default Pin for module:
#define DEFAULT_RST_PIN 9
#define DEFAULT_SPI_SS_PIN 10

//Default value
//in ms
#define DEFAULT_RESET_PERIOD 200
//in us
#define DEFAULT_REPLY_DELAY_TIME 7000

//sketch type (anchor or tag)
#define TAG 0
#define ANCHOR 1

//default timer delay
#define DEFAULT_TIMER_DELAY 80

//debug mode
#ifndef DEBUG
#define DEBUG false
#endif


class DW1000RangingClass {
public:
	//variables
	// data buffer
	static byte data[LEN_DATA];

	//initialisation
	static void    initCommunication(uint8_t myRST = DEFAULT_RST_PIN, uint8_t mySS = DEFAULT_SPI_SS_PIN, uint8_t myIRQ = 2);
	static void    configureNetwork(uint16_t deviceAddress, uint16_t networkId, const byte mode[]);
	static void    generalStart();
	static void    startAsAnchor(const char address[], const byte mode[], const bool randomShortAddress = true);
	static void    startAsTag(const char address[], const byte mode[], const bool randomShortAddress = true);
	static boolean addNetworkDevices(DW1000Device* device, boolean shortAddress);
	static boolean addNetworkDevices(DW1000Device* device);
	static void    removeNetworkDevices(int16_t index);

	//setters
	static void setReplyTime(uint16_t replyDelayTimeUs);
	static void setResetPeriod(uint32_t resetPeriod);

	//getters
	static byte* getCurrentAddress() { return _currentAddress; };

	static byte* getCurrentShortAddress() { return _currentShortAddress; };

	static uint8_t getNetworkDevicesNumber() { return _networkDevicesNumber; };

	//ranging functions
	static int16_t detectMessageType(const byte datas[]); // TODO check return type
	static void loop();
	static void useRangeFilter(boolean enabled);
	// Used for the smoothing algorithm (Exponential Moving Average). newValue must be >= 2. Default 15.
	static void setRangeFilterValue(uint16_t newValue);

	//Handlers:
	static void attachNewRange(void (* handleNewRange)(void)) { _handleNewRange = handleNewRange; };

	static void attachBlinkDevice(void (* handleBlinkDevice)(DW1000Device*)) { _handleBlinkDevice = handleBlinkDevice; };

	static void attachNewDevice(void (* handleNewDevice)(DW1000Device*)) { _handleNewDevice = handleNewDevice; };

	static void attachInactiveDevice(void (* handleInactiveDevice)(DW1000Device*)) { _handleInactiveDevice = handleInactiveDevice; };



	static DW1000Device* getDistantDevice();
	static DW1000Device* searchDistantDevice(const byte shortAddress[]);

	//FOR DEBUGGING
	static void visualizeDatas(const byte datas[]);


private:
	//other devices in the network
	static DW1000Device _networkDevices[MAX_DEVICES];
	static volatile uint8_t _networkDevicesNumber;
	static int16_t      _lastDistantDevice;
	static byte         _currentAddress[8];
	static byte         _currentShortAddress[2];
	static byte         _lastSentToShortAddress[2];
	static DW1000Mac    _globalMac;
	static int32_t      timer;
	static int16_t      counterForBlink;

	//Handlers:
	static void (* _handleNewRange)(void);
	static void (* _handleBlinkDevice)(DW1000Device*);
	static void (* _handleNewDevice)(DW1000Device*);
	static void (* _handleInactiveDevice)(DW1000Device*);

	//sketch type (tag or anchor)
	static int16_t          _type; //0 for tag and 1 for anchor
	// TODO check type, maybe enum?
	// message flow state
	static volatile byte    _expectedMsgId;
	// message sent/received state
	static volatile boolean _sentAck;
	static volatile boolean _receivedAck;
	// protocol error state
	static boolean          _protocolFailed;
	// reset line to the chip
	static uint8_t     _RST;
	static uint8_t     _SS;
	// watchdog and reset period
	static uint32_t    _lastActivity;
	static uint32_t    _resetPeriod;
	// reply times (same on both sides for symm. ranging)
	static uint16_t     _replyDelayTimeUS;
	//timer Tick delay
	static uint16_t     _timerDelay;
	// ranging counter (per second)
	static uint16_t     _successRangingCount;
	static uint32_t    _rangingCountPeriod;
	//ranging filter
	static volatile boolean _useRangeFilter;
	static uint16_t         _rangeFilterValue;
	//_bias correction
	static char  _bias_RSL[17]; // TODO remove or use
	//17*2=34 bytes in SRAM
	static int16_t _bias_PRF_16[17]; // TODO remove or use
	//17 bytes in SRAM
	static char  _bias_PRF_64[17]; // TODO remove or use


	//methods
	static void handleSent();
	static void handleReceived();
	static void noteActivity();
	static void resetInactive();

	//global functions:
	static void checkForReset();
	static void checkForInactiveDevices();
	static void copyShortAddress(byte address1[], const byte address2[]);

	//for ranging protocole (ANCHOR)
	static void transmitInit();
	static void transmit(const byte datas[]);
	static void transmit(const byte datas[], DW1000Time time);
	static void transmitBlink();
	static void transmitRangingInit(DW1000Device* myDistantDevice);
	static void transmitPollAck(DW1000Device* myDistantDevice);
	static void transmitRangeReport(DW1000Device* myDistantDevice);
	static void transmitRangeFailed(DW1000Device* myDistantDevice);
	static void receiver();

	//for ranging protocole (TAG)
	static void transmitPoll(DW1000Device* myDistantDevice);
	static void transmitRange(DW1000Device* myDistantDevice);

	//methods for range computation
	static void computeRangeAsymmetric(DW1000Device* myDistantDevice, DW1000Time* myTOF);

	static void timerTick();

	//Utils
	static float filterValue(float value, float previousValue, uint16_t numberOfElements);
};

extern DW1000RangingClass DW1000Ranging;

#endif

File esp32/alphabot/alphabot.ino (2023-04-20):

#include "TwoMotorDrive.h"
#include "StepperMotor.h"
#include "TFLunaObstacleScanner.h"
#include "DrivingAssistent.h"
#include "BLEHandler.h"
#include "config.h"
#include <esp32-hal-cpu.h>
#include <soc/soc.h>
#include <soc/rtc_cntl_reg.h>
#include "PositioningSystem.h"
#include <math.h>
#include "MotionTracker.h"
#include "Compass.h"
#include "WheelEncoderLeft.h"
#include "WheelEncoderRight.h"
#include "SaveFile.h"
#include "Navigator.h"
#include <BLECharacteristic.h>
#include "BLECharacteristicSender.h"
#include "PositioningKalmanFilter.h"
#include <algorithm>
#include <deque>
#include <Wire.h>

TwoMotorDrive* two_motor_drive = NULL;
StepperMotor* steering_stepper_motor = NULL;
DrivingAssistent* driving_assistent = NULL;
PositioningSystem* positioning_system = NULL;
MotionTracker* motion_tracker = NULL;
Compass* compass = NULL;
WheelEncoderLeft* left_wheel_encoder = NULL;
WheelEncoderRight* right_wheel_encoder = NULL;
TFLunaObstacleScanner* tfl_obstacle_scanner = NULL;
SaveFile* save_file = NULL;
Navigator* navigator = NULL;
PositioningKalmanFilter* posFilter = NULL;

float raw_dir = 0.0;
float dir = 0.0;
float anchor1_dist = 0.0;
float anchor2_dist = 0.0;
float anchor3_dist = 0.0;
float raw_pos_x = 0;
float raw_pos_y = 0;
float lps_x = 0;
float lps_y = 0;
int8_t drive_input_steer = 0;
int8_t drive_input_speed = 0;
std::deque<int8_t> front_obstacle_distance_angles_to_send_deque;

struct settings {
    uint8_t unused : 3;
    bool explore_mode : 1;
    bool navigation_mode : 1;
    bool collision_avoidance : 1;
    bool positioning : 1;
    bool invite : 1;
} settings;

struct logging {
    bool unused : 1;
    bool imu : 1;
    bool wheel_speed : 1;
    bool anchor_distances : 1;
    bool compass_direction : 1;
    bool pathfinder_path : 1;
    bool obstacle_distance : 1;
    bool positioning : 1;
} logging;

bool connected = false;
bool magnet_sensor_calibration = false;

BLEHandler* ble_handler = NULL;
BLECharacteristicSender* ble_char_toggle_sender = NULL;
BLECharacteristicSender* ble_char_add_obstacle_sender = NULL;

void charUpdateMotorsDataReceived(const char* data, size_t len) {
    if (len >= 2) {
        drive_input_speed = data[0];
        drive_input_steer = data[1];
    }
}

void charToggleDataReceived(const char* data, size_t len) {
    if (len >= 10) {
        static uint64_t last_toggle_send_time = 0;
        uint64_t send_time = *((uint64_t*)&(data[2]));

        if (last_toggle_send_time != send_time) {
            last_toggle_send_time = send_time;

            struct settings toggle_settings = *((struct settings*)data);
            struct logging toggle_logging = *((struct logging*)&(data[1]));

            if (settings.explore_mode != toggle_settings.explore_mode)
                settings.explore_mode = toggle_settings.explore_mode;

            if (settings.navigation_mode != toggle_settings.navigation_mode)
                settings.navigation_mode = toggle_settings.navigation_mode;

            if (settings.collision_avoidance != toggle_settings.collision_avoidance) {
                settings.collision_avoidance = toggle_settings.collision_avoidance;

                if (settings.collision_avoidance == false)
                    two_motor_drive->updateMotors(0, 0);
            }

            if (settings.positioning != toggle_settings.positioning)
                settings.positioning = toggle_settings.positioning;

            if (settings.invite != toggle_settings.invite) {
                settings.invite = toggle_settings.invite;

                if (settings.invite)
                    ble_handler->startAdvertising();
                else
                    ble_handler->stopAdvertising();
            }

            logging = toggle_logging;
        }
    }
}

void charToggleStateChanged(BLECharacteristicCallbacks::Status s, uint32_t code) {
    ble_char_toggle_sender->stateChanged(s, code);
}

void charPathfindingTargetDataReceived(const char* data, size_t len) {
    if (len >= 12) {
        static uint64_t last_pathfinding_target_send_time = 0;
        uint64_t send_time = *((uint64_t*)&(data[4]));

        if (last_pathfinding_target_send_time != send_time) {
            last_pathfinding_target_send_time = send_time;

            // Set target position
            int16_t target_x = data[0] | (data[1] << 8);
            int16_t target_y = data[2] | (data[3] << 8);
            navigator->setTarget(target_x, target_y);
            #ifdef DEBUG
            Serial.print("Set target position to: (");
            Serial.print(target_x);
            Serial.print(", \t");
            Serial.print(target_y);
            Serial.println(")");
            #endif
        }
    }
}

void charCalibrateDataReceived(const char* data, size_t len) {
    if (len >= 9) {
        static uint64_t last_calibrate_send_time = 0;
        uint64_t send_time = *((uint64_t*)&(data[1]));

        if (last_calibrate_send_time != send_time) {
            last_calibrate_send_time = send_time;

            switch (data[0]) {
                case 0: // Calibrate steering
                    steering_stepper_motor->calibrate();
                    break;
                case 1: // Automatic magnetometer calibration
                    // TODO: Automatic magnetometer calibration
                    break;
                case 2: // Begin manual magnetometer calibration
                    compass->beginMagnetSensorCalibration();
                    magnet_sensor_calibration = true;
                    break;
                case 3: // Finish magnetometer calibration
                    magnet_sensor_calibration = false;
                    compass->finishMagnetSensorCalibration();
                    save_file->setMagnetSensorCalibratedMinX(compass->getMinX());
                    save_file->setMagnetSensorCalibratedMaxX(compass->getMaxX());
                    save_file->setMagnetSensorCalibratedMinY(compass->getMinY());
                    save_file->setMagnetSensorCalibratedMaxY(compass->getMaxY());
                    save_file->setMagnetSensorCalibratedMinZ(compass->getMinZ());
                    save_file->setMagnetSensorCalibratedMaxZ(compass->getMaxZ());
                    save_file->write();
                    break;
                case 4: // Calibrate compass direction
                    float correct_dir = atan2(positioning_system->getAnc1Y() - lps_y, positioning_system->getAnc1X() - lps_x) * (180.0 / PI);
                    float compass_angle_offset = fmodf(correct_dir - raw_dir + 540.0, 360.0) - 180.0;
                    compass->setAngleOffset(compass_angle_offset);
                    save_file->setCompassAngleOffset(compass_angle_offset);
                    save_file->write();
                    break;
            }
        }
    }
}

static uint16_t next_obstacle_id = 0;

void charAddObstacleDataReceived(const char* data, size_t len) {
    if (len >= 16) {
        static uint64_t last_add_obstacle_send_time = 0;
        uint64_t send_time = *((uint64_t*)&(data[0]));

        if (last_add_obstacle_send_time != send_time) {
            last_add_obstacle_send_time = send_time;

            int16_t obstacle_x = data[8] | (data[9] << 8);
            int16_t obstacle_y = data[10] | (data[11] << 8);
            uint16_t obstacle_w = data[12] | (data[13] << 8);
            uint16_t obstacle_h = data[14] | (data[15] << 8);
            navigator->addObstacle(obstacle_x, obstacle_y, obstacle_w, obstacle_h, next_obstacle_id);

            uint8_t val[18];

            for (uint8_t i = 0; i < 16; ++i)
                val[i] = data[i];

            val[16] = next_obstacle_id;
            val[17] = next_obstacle_id >> 8;
            next_obstacle_id++;
            ble_char_add_obstacle_sender->sendValue(val, 18);
        }
    }
}

void charAddObstacleStateChanged(BLECharacteristicCallbacks::Status s, uint32_t code) {
    ble_char_add_obstacle_sender->stateChanged(s, code);
}

void charRemoveObstacleDataReceived(const char* data, size_t len) {
    if (len == 0) {
        // Clear obstacles
        navigator->clearObstacles();
        ble_handler->charRemoveObstacle->notify();
    } else {
        static uint64_t last_remove_obstacle_send_time = 0;
        uint64_t send_time = *((uint64_t*)&(data[0]));

        if (last_remove_obstacle_send_time != send_time) {
            last_remove_obstacle_send_time = send_time;

            if (len == 12) {
                // Remove obstacle by position
                int16_t x = data[8] | (data[9] << 8);
                int16_t y = data[10] | (data[11] << 8);
                navigator->removeObstacleByPosition(x, y);
                ble_handler->charRemoveObstacle->notify();
            } else if (len == 10) {
                // Remove obstacle by ID
                uint16_t id = data[8] | (data[9] << 8);
                navigator->removeObstacleById(id);
                ble_handler->charRemoveObstacle->notify();
            }
        }
    }
}

void charAnchorLocationsDataReceived(const char* data, size_t len) {
    if (len == 20) {
        static uint64_t last_anchor_locations_send_time = 0;
        uint64_t send_time = *((uint64_t*)&(data[0]));

        if (last_anchor_locations_send_time != send_time) {
            last_anchor_locations_send_time = send_time;

            int16_t anc1_x = data[8] | (data[9] << 8);
            int16_t anc1_y = data[10] | (data[11] << 8);
            int16_t anc2_x = data[12] | (data[13] << 8);
            int16_t anc2_y = data[14] | (data[15] << 8);
            int16_t anc3_x = data[16] | (data[17] << 8);
            int16_t anc3_y = data[18] | (data[19] << 8);
            positioning_system->setAnchorPositions(anc1_x, anc1_y, anc2_x, anc2_y, anc3_x, anc3_y);
        }
    }
}

void onCharToggleArrive() {
    #ifdef DEBUG
    Serial.println("Toggle arrived");
    #endif
}

void onCharAddObstacleArrive() {
    #ifdef DEBUG
    Serial.println("Add Obstacle arrived");
    #endif
}
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
void loop() {
    if (!connected) {
        delay(1000 / LOOP_FREQUENCY_HZ);
        return;
    }

    if ((loop_iteration % LOOP_FREQUENCY_HZ) == 0)
        time_last_second = millis();

    int8_t speed = two_motor_drive->getSpeed();

    if ((speed != 0 && signum(speed) != signum(moving_speed)) || abs(speed) > abs(moving_speed)) {
        moving_speed = speed;
    } else {
        bool signbit_before = std::signbit(moving_speed);
        moving_speed -= signum(moving_speed - speed) * (25.0 / LOOP_FREQUENCY_HZ);

        if (std::signbit(moving_speed) != signbit_before || abs(moving_speed) < abs(speed))
            moving_speed = speed;
    }

    if (logging.obstacle_distance || settings.collision_avoidance || settings.explore_mode) {
        int16_t angle = tfl_obstacle_scanner->scan();

        if (logging.obstacle_distance && angle >= 0) {
            if (angle >= 180)
                angle -= 360;

            // If element was not found, add it
            if (std::find(front_obstacle_distance_angles_to_send_deque.begin(), front_obstacle_distance_angles_to_send_deque.end(), angle) == front_obstacle_distance_angles_to_send_deque.end())
                front_obstacle_distance_angles_to_send_deque.push_back(angle);
        }
    }

    if (magnet_sensor_calibration)
        compass->magnetSensorCalibrate();

    if (logging.compass_direction || settings.positioning) {
        raw_dir = compass->getRawDirection();
        dir = fmodf(compass->getAngleOffset() + raw_dir + 360.0, 360.0);
    }

    if (settings.positioning) {
        posFilter->predict(1.0 / LOOP_FREQUENCY_HZ);

        double correctedSpeed = 0;
        int8_t absSpeed = std::abs(moving_speed);

        if (absSpeed > 45) {
            correctedSpeed = 0.0207 * absSpeed - 1.131 + std::pow(2.71828, -((absSpeed - 30) * 0.051 * (absSpeed - 30) * 0.051)) * 0.4;

            if (std::signbit(moving_speed))
                correctedSpeed = -correctedSpeed;
        }

        float left_wheel_mps = 0;
        float right_wheel_mps = 0;

        if (speed > 0) {
            left_wheel_mps = left_wheel_encoder->getWheelSpeedMps();
            right_wheel_mps = right_wheel_encoder->getWheelSpeedMps();
        } else if (speed < 0) {
            left_wheel_mps = -left_wheel_encoder->getWheelSpeedMps();
            right_wheel_mps = -right_wheel_encoder->getWheelSpeedMps();
        }

        float approximate_moving_speed_mps = (left_wheel_mps + right_wheel_mps) / 2.0;

        if (fabs(approximate_moving_speed_mps) < MIN_MOVING_SPEED_MPS)
            approximate_moving_speed_mps = 0;

        double vel[2];
        vel[0] = std::sin((90 - dir) * 0.017453292519943295) * ((4.0 * approximate_moving_speed_mps + correctedSpeed) / 5.0);
        vel[1] = std::cos((90 - dir) * 0.017453292519943295) * ((4.0 * approximate_moving_speed_mps + correctedSpeed) / 5.0);

        if (positioning_system->readDistances(&anchor1_dist, &anchor2_dist, &anchor3_dist)) {
            // New positioning data
            positioning_system->calculatePosition(anchor1_dist, anchor2_dist, anchor3_dist, &raw_pos_x, &raw_pos_y);
            double raw_pos[2] = { raw_pos_x / 100.0, raw_pos_y / 100.0 };
            posFilter->fusegps(raw_pos, POSITION_COVARIANCE, vel, VELOCITY_COVARIANCE);
        } else {
            posFilter->fusevel(vel, VELOCITY_COVARIANCE);
        }

        lps_x = posFilter->State.position[0] * 100.0;
        lps_y = posFilter->State.position[1] * 100.0;

        navigator->setOwnPosition(lps_x, lps_y);
        #ifdef DEBUG
        Serial.print("anchor1_dist: ");
        Serial.print(anchor1_dist);
        Serial.print("\tanchor2_dist: ");
        Serial.print(anchor2_dist);
        Serial.print("\tanchor3_dist: ");
        Serial.print(anchor3_dist);
        Serial.print("\tlps_x: ");
        Serial.print(lps_x);
        Serial.print("\tlps_y: ");
        Serial.println(lps_y);
        #endif

        if (logging.anchor_distances && (loop_iteration % (LOOP_FREQUENCY_HZ / 5)) == 0) {
            uint16_t vals[3];
            vals[0] = anchor1_dist;
            vals[1] = anchor2_dist;
            vals[2] = anchor3_dist;
            ble_handler->charAnchorDistances->setValue((uint8_t*)vals, 6);
            ble_handler->charAnchorDistances->notify();
        }
    }

    if (!(settings.positioning && settings.navigation_mode)) {
        if (settings.collision_avoidance) {
            driving_assistent->updateDistances(tfl_obstacle_scanner->getObstacleDistance(0),
                                               tfl_obstacle_scanner->getObstacleDistance(335),
                                               tfl_obstacle_scanner->getObstacleDistance(25),
                                               100);
            driving_assistent->updateSpeedAndSteer(two_motor_drive->getSpeed(), two_motor_drive->getSteerDirection());

            int8_t val_y = drive_input_speed;

            if (val_y > 0)
                val_y = driving_assistent->safeSpeedForward(val_y);
            else
                val_y = driving_assistent->safeSpeedBackward(val_y);

            two_motor_drive->updateMotors(drive_input_steer, val_y);
        } else {
            two_motor_drive->updateMotors(drive_input_steer, drive_input_speed);
        }
    }

    if ((logging.positioning || logging.compass_direction || logging.obstacle_distance) && (loop_iteration % (LOOP_FREQUENCY_HZ / 5)) == 1) {
        uint8_t sensor_logging_val[19];
        uint8_t sensor_logging_val_len = 2;
        uint8_t sensor_logging_counter = 0;
        sensor_logging_val[0] = 0;
        sensor_logging_val[1] = 0;

        if (logging.positioning) {
            sensor_logging_val[sensor_logging_val_len] = (uint8_t)lps_x;
            sensor_logging_val[sensor_logging_val_len + 1] = (((uint16_t)lps_x >> 8) & 0x07) | ((lps_x <= -1.0) << 3);
            sensor_logging_val[sensor_logging_val_len + 1] |= (uint8_t)lps_y << 4;
            sensor_logging_val[sensor_logging_val_len + 2] = (((uint16_t)lps_y >> 4) & 0x7F) | ((lps_y <= -1.0) << 7);
            sensor_logging_val_len += 3;
            sensor_logging_val[sensor_logging_counter / 4] |= 2 << ((sensor_logging_counter % 4) * 2);
            sensor_logging_counter++;
        }

        if (logging.compass_direction) {
            sensor_logging_val[sensor_logging_val_len] = (uint8_t)dir;
            sensor_logging_val[sensor_logging_val_len + 1] = (uint16_t)dir >> 8;
            sensor_logging_val_len += 2;
            sensor_logging_val[sensor_logging_counter / 4] |= 3 << ((sensor_logging_counter % 4) * 2);
            sensor_logging_counter++;
        }

        if (logging.obstacle_distance) {
            size_t number_of_sensor_values_to_send = min((size_t)(sizeof(sensor_logging_val) - sensor_logging_val_len) / 2, front_obstacle_distance_angles_to_send_deque.size());

            for (uint8_t i = 0; i < number_of_sensor_values_to_send; ++i) {
                int8_t angle = front_obstacle_distance_angles_to_send_deque.front();
                sensor_logging_val[sensor_logging_val_len] = angle;
                sensor_logging_val[sensor_logging_val_len + 1] = tfl_obstacle_scanner->getObstacleDistance((int16_t)angle + 360) / 2;
                sensor_logging_val_len += 2;
                sensor_logging_val[sensor_logging_counter / 4] |= 1 << ((sensor_logging_counter % 4) * 2);
                sensor_logging_counter++;
                front_obstacle_distance_angles_to_send_deque.pop_front();
            }
        }

        ble_handler->charSensor->setValue(sensor_logging_val, sensor_logging_val_len);
        ble_handler->charSensor->notify();
    }

    if (logging.imu) {
        // TODO: Implement IMU logging
    }

    if (logging.wheel_speed && (loop_iteration % (LOOP_FREQUENCY_HZ / 5)) == 2) {
        int8_t vals[2];
        int8_t left_speed = two_motor_drive->getLeftSpeed();

        if (left_speed > 0)
            vals[0] = min(left_wheel_encoder->getWheelSpeedMps() * 100.0, 127.0);
        else if (left_speed < 0)
            vals[0] = -min(left_wheel_encoder->getWheelSpeedMps() * 100.0, 127.0);
        else
            vals[0] = 0;

        int8_t right_speed = two_motor_drive->getRightSpeed();

        if (right_speed > 0)
            vals[1] = min(right_wheel_encoder->getWheelSpeedMps() * 100.0, 127.0);
        else if (right_speed < 0)
            vals[1] = -min(right_wheel_encoder->getWheelSpeedMps() * 100.0, 127.0);
        else
            vals[1] = 0;

        ble_handler->charWheelSpeed->setValue((uint8_t*)vals, 2);
        ble_handler->charWheelSpeed->notify();
    }

    uint32_t time_passed = millis() - time_last_second;
    uint32_t time_desired = (1000 / LOOP_FREQUENCY_HZ) * ((loop_iteration % LOOP_FREQUENCY_HZ) + 1);
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

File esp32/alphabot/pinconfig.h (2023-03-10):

#ifndef PINCONFIG_H
#define PINCONFIG_H

#define MOTOR_LEFT_FORWARD 23
#define MOTOR_LEFT_BACKWARD 19
#define MOTOR_LEFT_SPEED 5
#define MOTOR_LEFT_PWM_CHANNEL 0
#define MOTOR_RIGHT_FORWARD 17
#define MOTOR_RIGHT_BACKWARD 27
#define MOTOR_RIGHT_SPEED 14
#define MOTOR_RIGHT_PWM_CHANNEL 1
#define PWM_FREQ 30000
#define PWM_RESOLUTION 8

#define STEPPER_STEER_IN1 4
#define STEPPER_STEER_IN2 15
#define STEPPER_STEER_IN3 25
#define STEPPER_STEER_IN4 13

#define STEPPER_FRONT_IN1 26
#define STEPPER_FRONT_IN2 33
#define STEPPER_FRONT_IN3 32
#define STEPPER_FRONT_IN4 2

#define I2C_SDA 21
#define I2C_SCL 22

#define SERIAL2_RX 16

#define LEFT_WHEEL_ENCODER_D0 35
#define RIGHT_WHEEL_ENCODER_D0 34

#endif

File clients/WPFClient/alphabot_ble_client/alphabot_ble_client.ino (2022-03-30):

#include <Arduino.h>
#include <BLEDevice.h>
#include <BLEServer.h>
#include <BLE2902.h>

BLERemoteCharacteristic* char_sensor;
BLERemoteCharacteristic* char_pathfinding_target;
BLERemoteCharacteristic* char_add_obstacle;
BLERemoteCharacteristic* char_remove_obstacle;
BLERemoteCharacteristic* char_pathfinding_path;
BLERemoteCharacteristic* char_anchor_locations;

static void notifySensorCallback(
  BLERemoteCharacteristic* ble_remote_characteristic,
  uint8_t* data,
  size_t length,
  bool is_notify) {
    Serial.print("SENSOR: ");
    char buff[3];

    for (uint32_t i = 0; i < length; ++i) {
        sprintf(buff, "%02X", data[i]);
        Serial.print(buff);
    }

    Serial.println();
}

static void notifyPathfindingTargetCallback(
  BLERemoteCharacteristic* ble_remote_characteristic,
  uint8_t* data,
  size_t length,
  bool is_notify) {
    Serial.print("PATHFINDING_TARGET: ");
    char buff[3];

    for (uint32_t i = 0; i < length; ++i) {
        sprintf(buff, "%02X", data[i]);
        Serial.print(buff);
    }

    Serial.println();
}

static void notifyAddObstacleCallback(
  BLERemoteCharacteristic* ble_remote_characteristic,
  uint8_t* data,
  size_t length,
  bool is_notify) {
    if (length != 18)
        return;

    Serial.print("ADD_OBSTACLE: ");
    char buff[3];

    for (uint32_t i = 0; i < length; ++i) {
        sprintf(buff, "%02X", data[i]);
        Serial.print(buff);
    }

    Serial.println();
}

static void notifyRemoveObstacleCallback(
  BLERemoteCharacteristic* ble_remote_characteristic,
  uint8_t* data,
  size_t length,
  bool is_notify) {
    Serial.print("REMOVE_OBSTACLE: ");
    char buff[3];

    for (uint32_t i = 0; i < length; ++i) {
        sprintf(buff, "%02X", data[i]);
        Serial.print(buff);
    }

    Serial.println();
}

static void notifyPathfindingPathCallback(
  BLERemoteCharacteristic* ble_remote_characteristic,
  uint8_t* data,
  size_t length,
  bool is_notify) {
    Serial.print("PATHFINDING_PATH: ");
    char buff[3];

    for (uint32_t i = 0; i < length; ++i) {
        sprintf(buff, "%02X", data[i]);
        Serial.print(buff);
    }

    Serial.println();
}

static void notifyAnchorLocationsCallback(
  BLERemoteCharacteristic* ble_remote_characteristic,
  uint8_t* data,
  size_t length,
  bool is_notify) {
    Serial.print("ANCHOR_LOCATIONS: ");
    char buff[3];

    for (uint32_t i = 0; i < length; ++i) {
        sprintf(buff, "%02X", data[i]);
        Serial.print(buff);
    }

    Serial.println();
}

class MyClientCallback : public BLEClientCallbacks {
    void onConnect(BLEClient* client) {}

    void onDisconnect(BLEClient* client) {
        ESP.restart();
    }
};

void setup() {
    Serial.begin(115200);
    BLEDevice::init("");
    BLEClient* client = BLEDevice::createClient();
    client->setClientCallbacks(new MyClientCallback());
    Serial.println(" - Created client");

    while (!client->connect(BLEAddress("30:AE:A4:74:93:9A")))
        Serial.println(" - Failed to connect to Alphabot");

    Serial.println(" - Connected to Alphabot");

    BLERemoteService* remote_service = client->getService("4fafc201-1fb5-459e-8fcc-c5c9c331914b");

    if (remote_service == nullptr) {
        Serial.println(" - Could not find service");
        ESP.restart();
    }

    Serial.println(" - Found service");

    char_sensor = remote_service->getCharacteristic("4c999381-35e2-4af4-8443-ee8b9fe56ba0");

    if (char_sensor == nullptr) {
        Serial.println(" - Did not find SENSOR characteristic");
        ESP.restart();
    }

    Serial.println(" - Found SENSOR characteristic");

    char_sensor->registerForNotify(notifySensorCallback, true);
    Serial.println(" - Registered SENSOR characteristic for notify");

    char_pathfinding_target = remote_service->getCharacteristic("f56f0a15-52ae-4ad5-bfe1-557eed983618");

    if (char_pathfinding_target == nullptr) {
        Serial.println(" - Did not find PATHFINDING_TARGET characteristic");
        ESP.restart();
    }

    Serial.println(" - Found PATHFINDING_TARGET characteristic");

    char_pathfinding_target->registerForNotify(notifyPathfindingTargetCallback, true);
    Serial.println(" - Registered PATHFINDING_TARGET characteristic for notify");

    char_add_obstacle = remote_service->getCharacteristic("60db37c7-afeb-4d40-bb17-a19a07d6fc95");

    if (char_add_obstacle == nullptr) {
        Serial.println(" - Did not find ADD_OBSTACLE characteristic");
        ESP.restart();
    }

    Serial.println(" - Found ADD_OBSTACLE characteristic");

    char_add_obstacle->registerForNotify(notifyAddObstacleCallback, true);
    Serial.println(" - Registered ADD_OBSTACLE characteristic for notify");

    char_remove_obstacle = remote_service->getCharacteristic("6d43e0df-682b-45ef-abb7-814ecf475771");

    if (char_remove_obstacle == nullptr) {
        Serial.println(" - Did not find REMOVE_OBSTACLE characteristic");
        ESP.restart();
    }

    Serial.println(" - Found REMOVE_OBSTACLE characteristic");

    char_remove_obstacle->registerForNotify(notifyRemoveObstacleCallback, true);
    Serial.println(" - Registered REMOVE_OBSTACLE characteristic for notify");

    char_pathfinding_path = remote_service->getCharacteristic("8dad4c9a-1a1c-4a42-a522-ded592f4ed99");

    if (char_pathfinding_path == nullptr) {
        Serial.println(" - Did not find PATHFINDING_PATH characteristic");
        ESP.restart();
    }

    Serial.println(" - Found PATHFINDING_PATH characteristic");
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

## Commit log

2021-08-21 Widen the DWM1000 adapter board
    Widen the DWM1000 adapter board so that 10 mm ground plane is available
    on each side next to the DWM1000 module to achieve the best vertically
    polarised radiation pattern.
2021-08-24 Unify line endings to LF (#9)
    [centroid.csv]
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2021-08-26 dwm1000_anchor/tag: Improve positioning accuracy (#11)
    Improve the accuracy of the positioning system by switching to UWB
    channel 7. Also adjust the antenna delay accordingly.
2021-08-26 rpi/sd_image: Switch the apt release to buster (#12)
    Switch the apt release from sid to buster to get stable releases instead
    of bleeding-edge packages.
2021-08-26 esp32: Use forward slashes in include paths (#13)
    Always use forward slahes in the path when including header files,
    otherwise builds fail on Linux.
    [alphabot.ino]
2021-09-07 esp32/PrimaryESP32: Refactor StepperMotor (#16)
    Make member variables private and make stepperTask function part of the
    StepperMotor class.
2021-09-07 esp32/PrimaryESP32: Fix compiler warnings (#17)
    Fix compiler warnings by adding a 'U' suffix to unsigned integers.
2021-09-07 rpi/sd_image: Replace systemd-timesyncd with chrony (#20)
    Use chrony instead of systemd-timesyncd as the NTP client to get the
    current time.
2021-09-25 rpi/sd_image: Setup WiFi access point (#25)
    Set up a WiFi access point on the Raspberry Pi along with a DHCP and
    DNS server.
2021-09-29 pcb: Fix RSTn pin on the DWM1000 adapter board (#33)
    Sever the connection between the RSTn pin of the DWM1000 module and
    ground to avoid continuously resetting the chip.
2021-09-29 pcb: Add DWM1000 to its adapter assembly files (#10)
    Add the DWM1000 module to the assembly files of the DWM1000 adapter
    board.
    [DecawaveProMiniAdapter_BOM_PCBWay.xlsx, centroid.csv]
2021-09-29 stl: Add DWM1000 adapter board mounts (#24)
    [dwm1000.anchor.adapter.board.mount.stl, dwm1000.tag.adapter.board.mount.stl]
2021-11-02 esp32/PrimaryESP32: Make some member functions const (#39)
    Add the const keyword to class member functions that do not modify the
    called object.
2021-11-07 esp32/PrimaryESP32: Fix inverted differential (#41)
    [TwoMotorDrive.cpp]
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2021-11-08 docs: Add timestamps to BLE protocol specification (#43)
    Add time stamps to BLE characteristics which should arrive in the
    correct order and might be re-sent by the client if the server does not
    respond within a specified time frame.
2021-11-14 esp32/PrimaryESP32: Expose BLE service (#45)
    Advertise the BLE service UUID to improve support with other clients.
2021-11-14 esp32/PrimaryESP32: Fix inverted speed in Navigator (#46)
    Fix Alphabot driving in the wrong direction when navigating to a target.
    [Navigator.cpp]
2021-12-07 rpi/sd_image: Free up ttyS1 serial port (#59)
    Change the serial port of the console to serial0 and free up ttyS1 for
    other serial devices (e.g. a positioning tag) that may be connected to
    the Raspberry Pi via GPIO pins 14 and 15.
2021-12-08 pcb: Add Alphabot ESP32 PCB (#31)
    Replace most of the wiring of the ESP32 version of the Alphabot with a
    printed circuit board to make it more manageable and to avoid loose
    connections.
    [AlphabotESP32PCB_BOM_PCBWay.xlsx, centroid.csv]
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2021-12-29 docs/protocol: Remove duplicate calibration request (#72)
    Remove the compass calibration setting from the settings bit field,
    as the compass can already be calibrated in another way.
2022-01-01 docs/clients: Add missing sensor responses (#71)
    Add protocol documentation, code implementation and unit test cases for
    5 new sensor responses:
    * Wheel speed
    * Anchor distances
    * Accelerometer (IMU)
    * Gyroscope (IMU)
    * Magnetometer (IMU)
2022-01-02 clients: Add Xamarin app (#76)
    Xamarin App for UWP and Android.
    Features:
    * gyroscope control
    * positioning system
    * toggles
    * automatic pinging in background
2022-01-03 Refactor Alphabot.NET with present functionality (#66)
    Working Requests:
    * Speed
    * Steer
    * Calibrate
    * Ping
    * Toggle (DoPositioning, LogPositioning, DoCollisionAvoidance)
    Working Responses:
    * Ping
    * Toggle (DoPositioning, LogPositioning, DoCollisionAvoidance)
    * Positioning
    * Error
    Also fixed app crash, when executed on a non GPIO device.
2022-01-05 docs: Add second wheel speed (#79)
    Add second wheel speed in protocol, client library and unit test.
2022-01-25 docs/protocol: Improve the wheel speed resolution (#82)
    Send the wheel speed with a higher resolution to be able to represent
    the small values on a reasonable scale.
2022-03-20 stl: Add LiDAR bumper (#84)
    [bumper.lidar.front.stl, bumper.lidar.holder.stl]
2022-03-24 emulator_rpi: Fix wrong GPIO memory offset (#89)
    Fix wrong GPIO memory offset when accessing a GPIO pin above 31.
2022-08-22 esp32/PrimaryESP: Fix compile error with Wire 2.0.0 (#90)
    Fix compile error when using version 2.0.0 of the Wire library
    [alphabot.ino]
2022-08-23 esp32/PrimaryESP32: Fix position & compass logging (#91)
    Fix incorrect format of position and compass data when logging sensors.
    [alphabot.ino]
2022-08-24 clients/android: Fix sensor data interpretation (#92)
    Fix incorrect interpretation of received position and compass data.
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2022-09-01 esp32/PrimaryESP32: Move StepperMotor task to ULP (#94)
    Move the StepperMotor task to the Ultra Low Power (ULP) coprocessor of
    the ESP32. This reduces the load on the main processor while still
    ensuring that the steering task runs smoothly.
2022-09-22 esp32/PrimaryESP: Fix wrong position data (#95)
    Fix mistakenly transmiting -2048 when the value of an axis is between
    0 and -1.
    [alphabot.ino]
2022-09-22 esp32/PrimaryESP: Fix Pathfinder map dimensions (#98)
    If the start position or the target are at the top or left edge of the
    map, the map dimensions may be too small. This could lead to heap
    corruption later on.
    [Pathfinder.cpp]
2022-09-22 esp32/PrimaryESP: Increase I2C speed to 400 kbps (#99)
    By increasing the I2C speed, the ESP32 has to wait less to read data
    from I2C devices. This in turn leaves more time for other operations.
2022-09-22 esp32/PrimaryESP: Initialize members in constructors (#100)
    Initialize class members with default values.
2022-09-22 esp32/PrimaryESP: Add sensor switches to MotionTracker (#101)
    Make the MotionTracker configurable through the constructor.
2022-09-22 esp32/PrimaryESP: Increase max ICM20948 I2C transfer size (#102)
    Increase the maximum read/write size that is used for I2C communication
    with the ICM-20948 chip. This makes the read/write processes a bit
    faster.
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2022-09-22 esp32/PrimaryESP: Add linear acceleration to MotionTracker (#104)
    Linear acceleration refers to the readings of the accelerometer without
    the gravitation.
2022-09-22 esp32/PrimaryESP: Filter ranges in PositioningSystem (#105)
    Filter out garbage data received from the positioning module.
2022-09-23 esp32/PrimaryESP: Optimize position calculation (#106)
    Optimize a duplicate 2D vector normalization by caching the result.
2022-09-23 esp32/PrimaryESP: Round properly in Pathfinder (#107)
    This way the rounded values will overall be closer to the original
    values.
2022-09-23 esp32/PrimaryESP: Fix Pathfinder path missing the start coordinate (#108)
    [Navigator.cpp, Pathfinder.cpp]
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2022-09-25 esp32/PrimaryESP: Improve Navigator (#113)
    Prevent the Alphabot from trembling in place when navigating in some
    cases. Also prevent collisions with obstacles.
    [Navigator.cpp, config.h]
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2022-11-03 esp32/PrimaryESP: Fix overflow when logging too long Pathfinder path (#122)
    [alphabot.ino]
2022-11-03 esp32/PrimaryESP32: Fix Pathfinder inefficiency (#123)
    Fix Pathfinder inefficiency of adding duplicates of untested nodes to
    the list of untested nodes. Fixing this issue significantly improves
    memory usage and performance.
    [Pathfinder.cpp]
2022-11-03 esp32/PrimaryESP: Preallocate nodes buffer of Pathfinder (#124)
    Allocate the nodes buffer of the Pathfinder when instantiating the
    Pathfinder. This way, the buffer does not have to be allocated and freed
    repeatedly. This fixes the problem of not having a large enough
    continuous block of memory on the heap.
    [Pathfinder.cpp]
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2022-11-18 pcb: Update Alphabot ESP32 PCB (#116)
    Remove the secondary ESP32 from the PCB and add a 5V voltage regulator
    to the board to convert the supplied 12V to 5V. Also add the stepper
    controller directly to the board.
    [AlphabotESP32PCB_BOM_PCBWay.xlsx, centroid.csv]
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2022-11-18 stl: Simplify the LiDAR front bumper (#119)
    Simplify the bumper because the ULN2003 breakout board at the front is
    no longer needed.
    [bumper.lidar.front.stl]
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2022-11-18 stl: Add a wheel encoder (#127)
    [wheel.encoder.stl]
2022-12-18 Remove outdated wiring diagrams (#132)
    [wiring_esp32.fzz, wiring_rpi.fzz]
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2023-01-06 stl: Make place for a second wheel encoder (#137)
    [wheel.encoder.stl]
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2023-02-05 esp32/PrimaryESP: Specify platform version in platformio.ini (#150)
    Specify the platform version in platformio.ini to prevent bugs caused
    by breaking changes from future versions.
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2023-03-13 esp32/PrimaryESP32: Fix spelling error in comment (#157)
    [Navigator.cpp]
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2023-03-13 esp32: Fix bad bit shift when adding an obstacle (#160)
    [alphabot.ino]
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
